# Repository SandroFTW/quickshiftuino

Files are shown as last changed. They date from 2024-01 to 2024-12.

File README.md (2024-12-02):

# quickshiftuino
## Latest development (edited 02.10.2024)
The third revision (R3) PCB is done and ordered. I added Molex Picoblade connectors to the board for two hall sensor connections without soldering. The dimensions increased slightly from 35x40mm to 42x40mm.
Vias are now also tented to prevent short circuits between Quickshiftuino PCB and the piggyback ESP32 Mini.
Currently I'm developing a hall pressure sensor that mounts at one end of the shift rod. 3D printed prototypes already give promising results, aluminium CNC milled parts are going to arrive in 2 weeks.

Gerber files will be available after I did some testing.

Previous R2 PCB that's almost the same as R3:

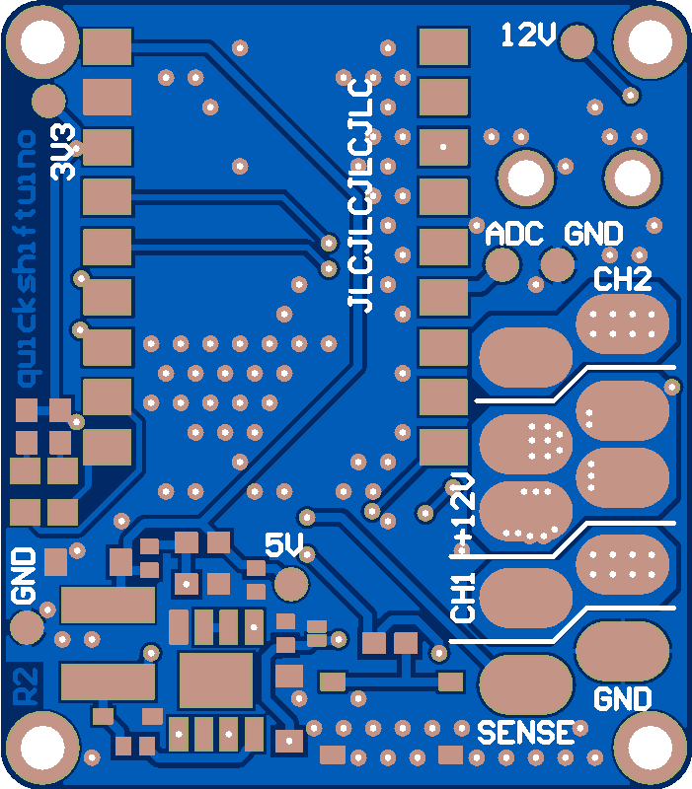
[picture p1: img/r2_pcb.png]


<br>

## Overview
Quickshiftuino is a simple device that detects the shift motion in the gear lever linkage and cuts the ignition coil power for a specified time.
This enables clutchless upshifting (and in some situations downshifting) by unloading the gearbox and drivetrain.

The cutoff time is dependant on engine RPM and is linearly scaled bewtween the lowest RPM (minRPM) and highest RPM (maxPRM).
An alternative to fixed cut-times would be a hall sensor and magnet mounted to the gearbox shift shaft to detect once the gearbox dog rings are touching or fully engaged.

My main idea was to keep it simple to use and universal. In total there are 6 possible configurations that have different advantages and disadvantages.

Configuration is possible though a locally hosted web-interface. Simply connect to the WiFi network provided by the device.
http://192.168.4.1/ gives access to the config page.
http://192.168.4.1/debug.html/ shows output values of the selected sensors and the current RPM value. This is helpful for finetuning parameters.

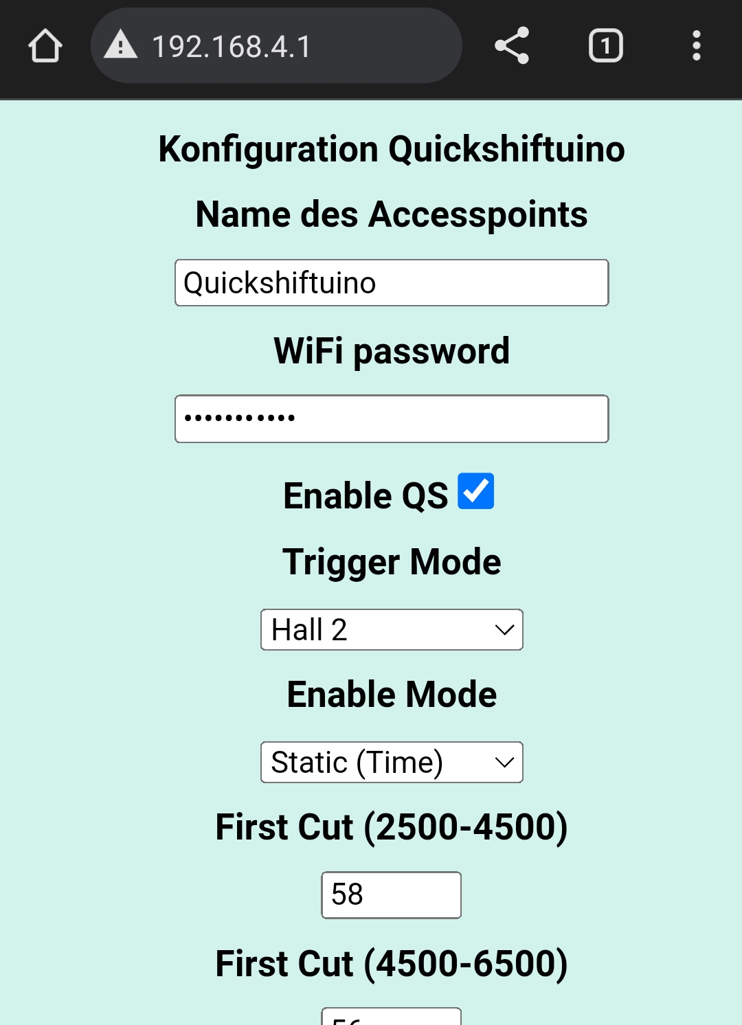
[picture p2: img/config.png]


<br>

The R1 PCB had a few issues with the power switching logic (high side P-MOS was wired incorrectly):

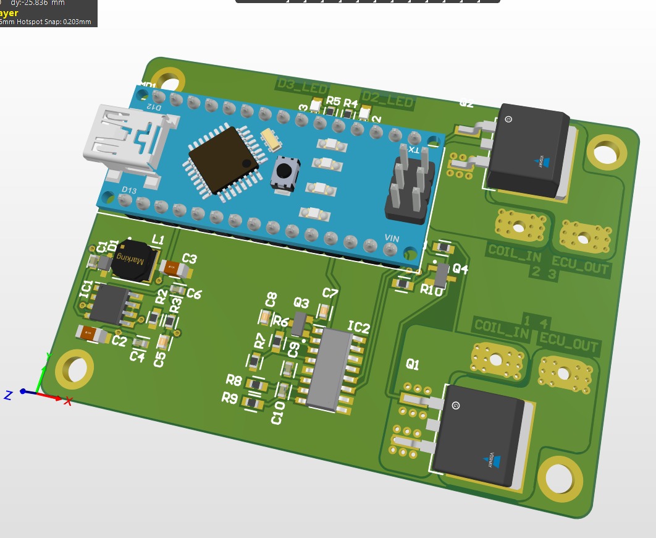
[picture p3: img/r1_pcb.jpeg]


For R2 many little bugs were resolved and the size drastically reduced.
The MCU was also switched from an Arduino Nano to a much more powerful and compact ESP32 Mini (Waveshare).

<br>

## Shift detection
Shift lever pressure can be measured in two different ways with quickshiftuino.

  ### 1. Piezo quickshifter sensor
  These sensors are all around Aliexpress if you search for quickshifter parts. A few big companies are using something similar with success already.
  This sensor doesn't react to force but it detects force change or momentum. The applied force can be more than enough but the sensor doesn't output a big voltage if you're shifting really soft and slow.
  The main drawback is that it only gives reliable results when mounted on the gearbox shaft clamp. That way there won't be a signal difference between up- and downshifts though. Installation is probably the easiest out of all.
  
  ### 2. Hall Sensor pressure sensor
  This is the latest option and still under development. Current tests show really good results and easy setup. The required parts are a bit pricier than the Piezo sensor though. A hall sensor measures the movement of a spring loaded mechanism that's mounted in the shift rod. Due to it being fairly low profile a modification of the shift rod might not be required on many bikes.

  ### 3. Load cell (not supported yet)
  The PCB features an HX711 load cell amplifier circuit.
  A DYMH-103 load cell needs to be installed in the shift rod to sense actual force.
  This method is more complex since in most cases the shift rod needs to be cut and modified but you will also get more consistent results.
  Another benefit is that up- and downshifts are clearly distinguishable because of positive and negative readings.

<br>

## Future plans
  ### Software ToDo's
  - Add hysteresis for hall sensor pressure sensor to prevent continuous triggering when holding the shift lever up in top gear
  - Instead of measuring ignition pulses in a fixed timespan: Set up timer that resets with each ignition pulse (RPM way more precise and faster update rate)
  - Long term: Improve efficiency of config GUI code and move all non-quickshifter tasks to second MCU core (enables faster loop times, probably not necessary)
  - Fun project: 2-step RPM limiter for launch control or just cool flames out of the exhaust (relies on quick and precise RPM measurement)
  - Fun project: Add support for shift indicator LED using free GPIO pad on R3 PCB (could also be used for other practical indicators)
  ### Hardware
  - Use N-Mos instead of P-Mos (requires high side driver, e.g. DZDH0401DW-7, current total voltage drop ~0.3V, maybe 0.1V possible)

The current design might cause unwanted pre-ignition if the coil power is cut during the dwell time. I haven't noticed this happening but there would be 2 approaches to prevent this:
- Switch to a N-Mos pull down design that overrides the ECU signal and keeps the coil pulled low (less complicated wiring but more heat/current in the coil)
- Only allow ignition cuts for a certain time after the coil has fired (maybe even RPM based, keeps current hardware)
  
Currently I am working on the second revision of the PCB which will have a few major issues resolved (mainly power switching logic).
I'm also thinking about either switching to an ESP32 MCU or adding a bluetooth module to the PCB. This should enable changing configuration values without the need for a computer and Arduino IDE.

The V1 PCB design will be added and I will upload a few pictures and videos of the project in a few weeks.

First test in the garage as a proof of concept: Video[https://youtu.be/FZ6roKEg_gY]

## Dependencies
- ESPAsyncWebServer (https://github.com/me-no-dev/ESPAsyncWebServer)
- AsyncWebConfig (https://github.com/GerLech/AsyncWebConfig/)
- AsyncTCP (https://github.com/dvarrel/AsyncTCP)
- WebSockets (https://github.com/Links2004/arduinoWebSockets)

AsyncWebConfig requires changing MAXVALUES in the header file from 20 to 30!; https://github.com/GerLech/AsyncWebConfig/blob/main/src/AsyncWebConfig.h#L32
Don't use the ESPAsyncWebServer from the library manager, you need to manually install the one by me-no-dev.

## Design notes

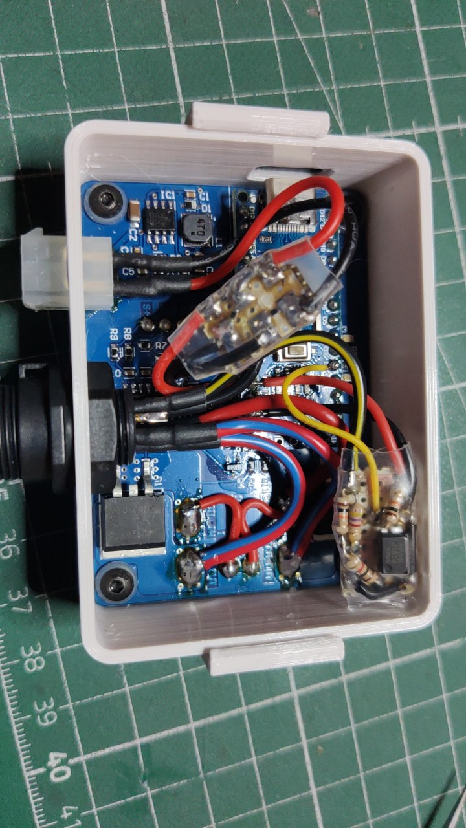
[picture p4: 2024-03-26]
img/r1_electronics.jpg

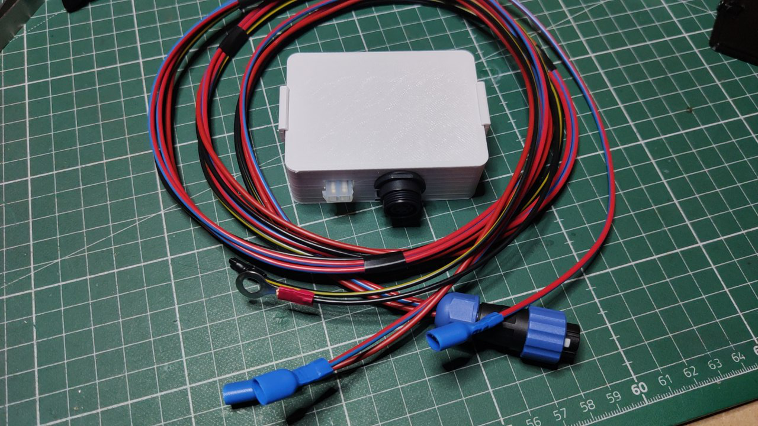
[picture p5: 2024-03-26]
img/r1_harness.jpg

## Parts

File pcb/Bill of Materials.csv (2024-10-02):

Comment | Description | Designator | Quantity
PC81710NIP1B | Attenuator or Isolator | AT1 | 1
C0603C104K3PACTU | C0603 0.10 µF X5R 30ppm/°C 10.00% 25 V | C1, C4, C6, C9, C10 | 5
C3216X5R1E476M160AC | Multilayer Ceramic Capacitors 47uF ±20% 25V X5R SMD 1206 | C2, C3 | 2
C0603C225K4PACTU | CAP CER 2.2UF 16V X5R 0603 | C5 | 1
C0603C106M8PACTU | CAP CER 10UF 10V X5R 0603 | C7, C8 | 2
C0603C333K1RECAUTO | C0603C333K1RECAUTO 0603 (1608METRIC) Ceramic Capacitor Esd SMD Auto X7R 100V 0.033MUF ±10% X7R | C11 | 1
C0603C473K3RACTU | CAP CER 0.047UF 25V 10% X7R 0603 | C12 | 1
CL10A105KA8NNNC | Cap Ceramic 1uF 25V X5R ±10% Pad SMD 0603 +85°C T/R | C13, C14 | 2
BAT165 | Medium Power AF Schottky Diode, SOD323, Reel, Green | D1 | 1
150080RS75000 |  | D2 | 1
150080GS75000 |  | D3 | 1
D20V0L1B2WS-7 | TVS Diode (Bi-directional) | D4, D7, D8 | 3
824521331 | 824521331 TVS diode [Würth Elektronik] 824521331 TVS diode | D5, D6 | 2
MP9486GN-Z | Integrated Circuit | IC1 | 1
HX711 | Integrated Circuit | IC2 | 1
Waveshare ESP32-S3 Mini | WaveShare ESP32-S3 Mini Development Board ESP32-S3FH4R2 240MHz 2.4GHz Wi-Fi Bluetooth 5 | IC4 | 1
53261-0371 | CONN HEADER SMD R/A 3POS 1.25MM | J1, J2 | 2
74404052470 | 74404052470 Inductors, Fixed, WE-LQS SMD 5020 47uH 0.8A 521mOhms | L1 | 1
SQJ459EP-T1_GE3 | MOSFET P-CH 60V 52A POWERPAKSO-8 | Q1, Q2 | 2
MMBT4403LT1G | Switching Transistor, PNP Silicon, 3-Pin SOT-23, Pb-Free, Tape and Reel | Q3 | 1
2N7002 | N-Channel OptiMOS Small-Signal-Transistor, 60 V VDS, 0.3 A ID, -55 to 150 degC, PG-SOT23, Reel, Green | Q4, Q5 | 2
CRCW060310K0FKEC | RES Thick Film, 10kO, 1%, 0.1W, 100ppm/°C, 0603 | R1, R2, R6, R10, R11, R12, R13, R16, R18, R19, R21 | 11
CRCW0603240KFKEA | RES Thick Film, 240kO, 1%, 0.1W, 100ppm/°C, 0603 | R3 | 1
CRCW0603100RFKEB | RES Thick Film, 100O, 1%, 0.1W, 100ppm/°C, 0603 | R4, R5, R8, R9 | 4
CRCW06038K20FKEC | RES Thick Film, 8.2kO, 1%, 0.1W, 100ppm/°C, 0603 | R7 | 1
CRCW06033K30FKEA | RES Thick Film, 3.3kO, 1%, 0.1W, 100ppm/°C, 0603 | R14, R22 | 2
0 Ohm Jumper | RES Thick Film, 0O, 5%, 0.33W, 200ppm/°C, 0603 | R15 | 1
RMCF0603FT2K20 | 2.2kO ±1% 0.1W 0603 Thick Film Chip Resistor AEC-Q200 compliant | R17 | 1
CRCW06032M00FKEA | RES Thick Film, 2MO, 1%, 0.1W, 100ppm/°C, 0603 | R20 | 1
CRCW060320K0FKEA | RES Thick Film, 20kO, 1%, 0.1W, 100ppm/°C, 0603 | R23, R24 | 2

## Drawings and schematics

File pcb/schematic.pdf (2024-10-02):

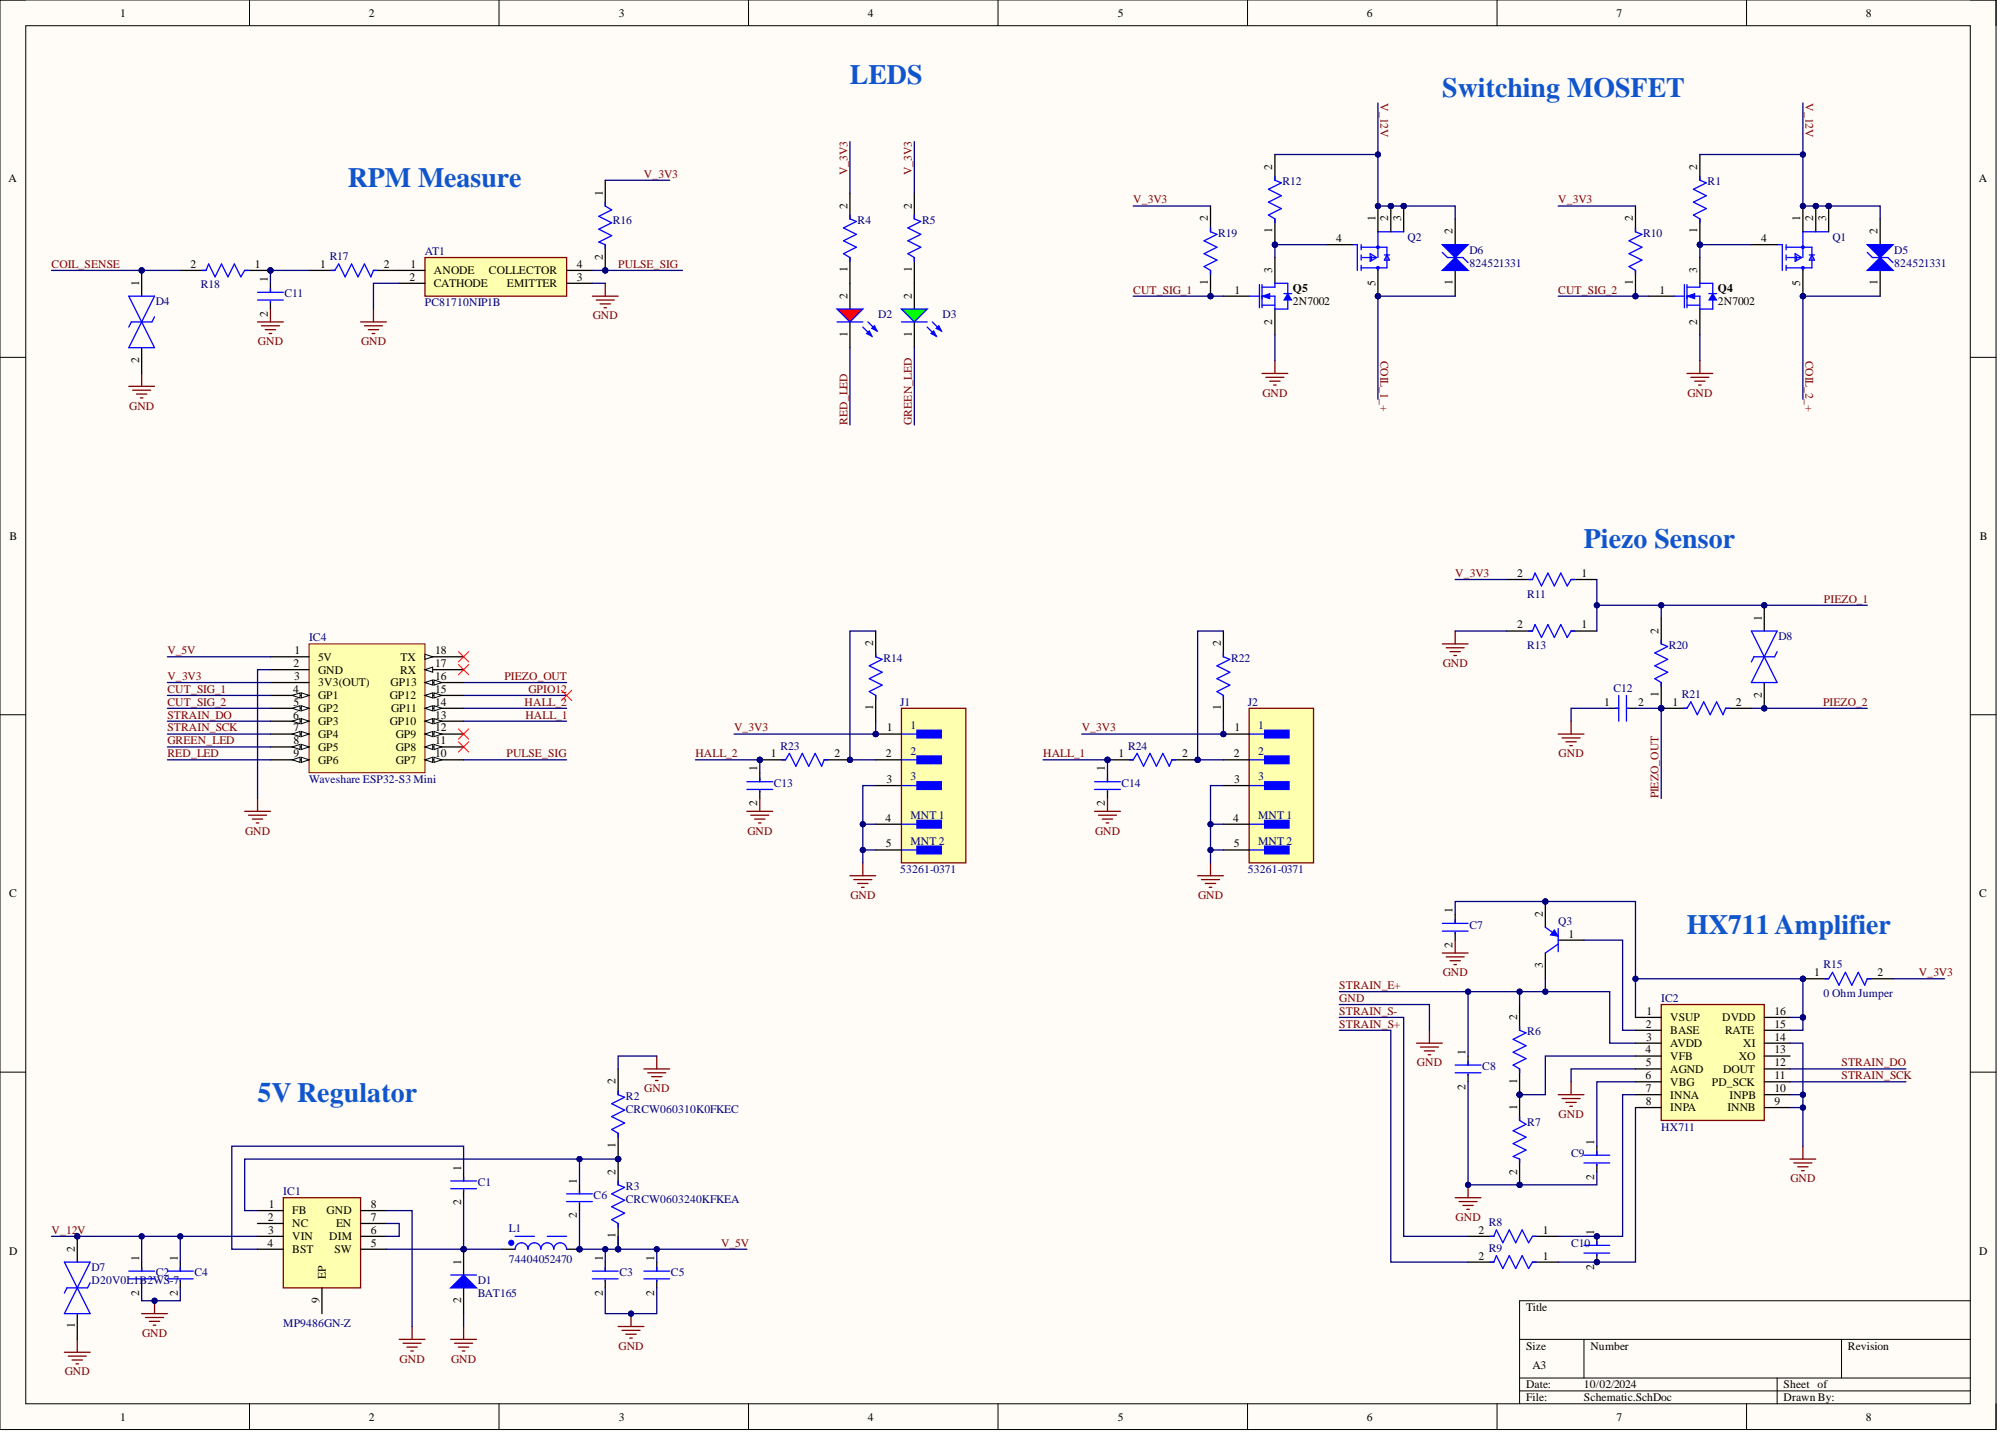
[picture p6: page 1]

VBG 6
INNA 7
INPA 8

GND C9

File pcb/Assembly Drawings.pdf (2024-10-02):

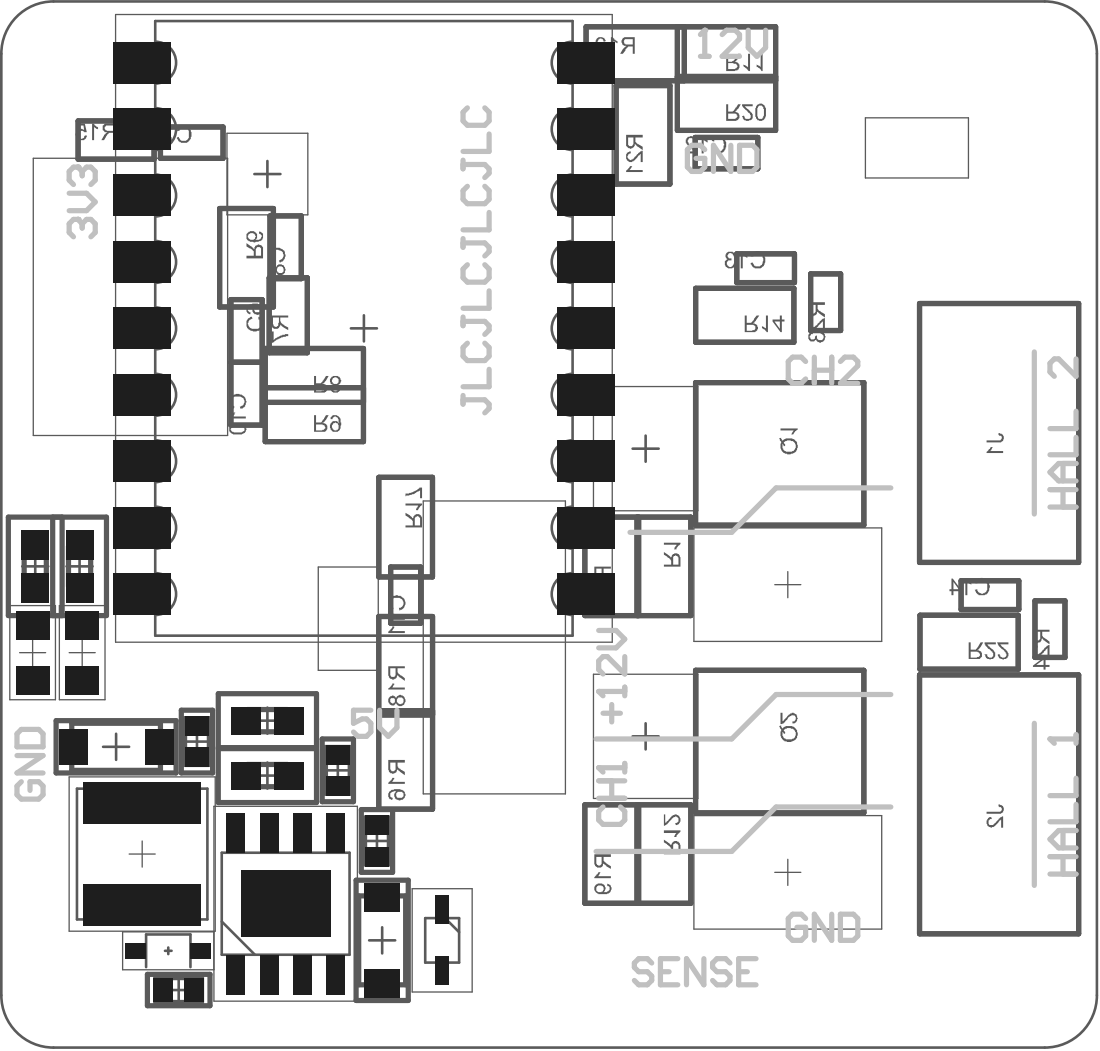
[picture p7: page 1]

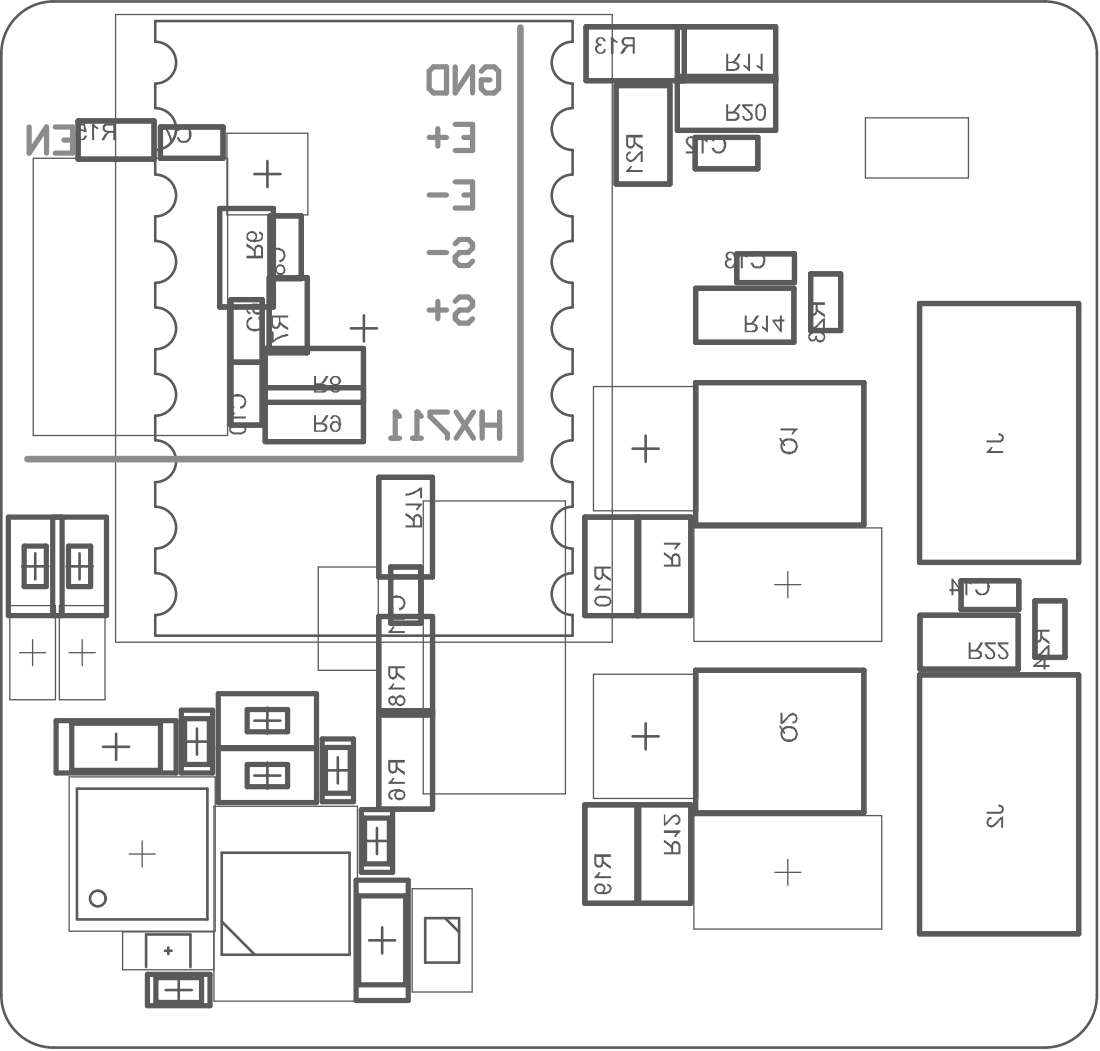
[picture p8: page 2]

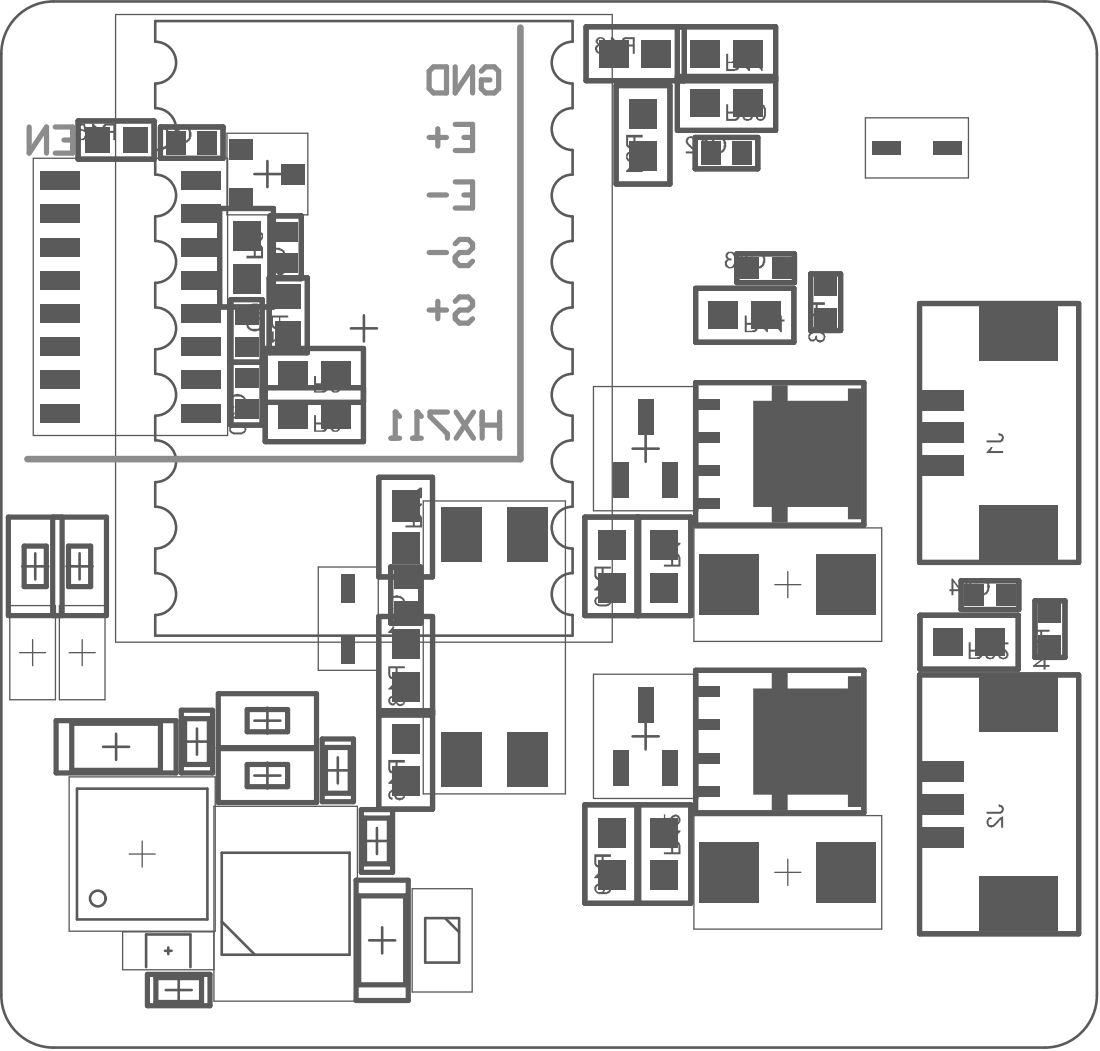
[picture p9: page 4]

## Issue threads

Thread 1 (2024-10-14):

SPECIFIC

Riccardo-Adami, 2024-10-14:
/I wanted to do the same, can i do the same using areduino nano or arduino one? what calbs do i need? how can i implement the logic of the button when pressed? how can i return energy to the candle and other few questions, thanks for your time.
(i can write you on email if i can find one).

SandroFTW, 2024-10-14:
Hi,
you can take a look at the R1 release files and schematic. R1 used an Arduino Nano and worked totally fine.

I assume "button" refers to the sensor that detects the upshift motion? The easiest way to add that is the piezo sensor listed in the readme file. It only requires one screw to be changed and no further modifications to the bike.

Quickshiftuino uses a pMOS right now to simplify the circuit. In theory an nMOS with a driver circuit would reduce the losses due to resistance but the coil only draws ~10-15A usually which is less than 0.3V voltage drop (from your 12V battery voltage). Might be a consideration for the future to change that.

Feel free to ask if you have further questions.

Riccardo-Adami, 2024-10-14:
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

thank you very much for the quick answer, I was wondering if on a bike with less power and no rods, it would still be okay. By “button” I was referring to a button/sensor placed under the shift lever tip that would send a signal to the arduino (arduino one or arduino nano, what do you recommend?) and this would interrupt for a temppo timespan (like 70 milliseconds) the current given to the spark plug, and once the 70 milliseconds was over it would resume the current flow
Still thx for the clear response :)

SandroFTW, 2024-10-15:
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

What you're describing would be the absolute minimum requirements.
A button is probably not enough for smooth operation. You need a sensor that only triggers once a certain force is applied to the shift lever so it's preloaded (~5-10kg on the lever).
[Piezo pressure sensor](https://aliexpress.com/item/1005004447507076.html) & [Fitting Connector, 2p](https://aliexpress.com/item/1005001706480040.html)
This is the sensor I suggest. If you place this on the clamping part that attaches the shift lever to the gearbox shaft you get a signal based on the force you apply to the lever.

Once it senses enough preload pressure you can cut the power for 70ms and it will probably shift without issues.
It probably won't be very smooth though. On my bike (Yamaha XJ6 4 cylinder) the optimal time is between 54ms for low RPM and 62ms for high RPM. A few ms difference already make quite a difference. That's why I'm changing the time based on RPM.

To get it really smooth you can also use a hall sensor that measures the position of the gearbox shaft. This indicates once the gear is fully engaged and tells the arduino to enable power again.

Riccardo-Adami, 2024-10-15:
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

Yeah sure, thx a lot for the response. For the first model I ordered an Arduino Nano, relay, breadboard, a pressure button, just for a quick test. My moto is a single cylinder one, derby. I was thinking of putting it under the crank, so when it's pushed, only up, It will send a signal to the Arduino nano (I'm doing it with that, should i use the Arduino 1 instead?) and it will be connected to the relay which will turn off the power only when the button provides the signal, am I doing right? thx for ur time (:

SandroFTW, 2024-10-15:
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

Sounds good, Arduino Nano is fine. Make sure to include a dead time between power cuts or your engine will just switch of when finding neutral ^^

riccio8, 2024-10-15:
Yeah i was thinking about 20 mills, is it fine? btw the first test is only for up shifting, thx mate

SandroFTW, 2024-10-15:
> Yeah i was thinking about 20 mills, is it fine? btw the first test is only for up shifting, thx mate (that's my main account sry )

Your single cylinder engine only fires about every 50 ms assuming 1200 RPM idle. So there's a high change it just doesn't notice the 20ms power on.

I have it at 350ms which is just a bit less than the fastest interval that I'm upshifting.

riccio8, 2024-10-15:
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

yeh yeah I meant it, 350ms aren't too much? just asking, I was thinking of doing it with 70ms per up shifting (is it is okay Right?) and 20 between the number of the up shifting

SandroFTW, 2024-10-15:
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

Sorry if I wasn't precise enough.

After you press the button it should wait for ~20ms until disabling power, then disable for ~70ms. After enabling it shouldn't react to another button press for ~350ms so it doesn't get stuck in a loop and kill the engine for example if you're in top gear and holding the lever up. Also a flag that disables another cutoff interval if you haven't released the lever yet is helpful.

Just sharing my experience since I already came across all these bugs in the last year that I've been working on this project :p

riccio8, 2024-10-15:
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

yeah yeah thx a lot, you were very clear and complete. Now I will see how the project goes and if I have other doubts I will definitely write to you, thank you very much

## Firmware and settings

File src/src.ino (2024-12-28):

#include <WebSocketsServer.h>
#include <ESPAsyncWebServer.h>
#include <AsyncWebConfig.h>
#include <AsyncTCP.h>
#include <SPIFFS.h>
#include <WiFi.h>

// TODO: Check if lever moved from zero position after 20 ms otherwise cancel shift
// -> Almost done, add more config options for tuning

// waitHyst feature not compatible with piezo sensor

// Make LED functions more useful (green led shift pressure indicator, red led rpm)

WebSocketsServer webSocket = WebSocketsServer(81);

// MAIN CONFIGURATION
#define loopTime         2    // 500 Hz

// PIN DEFINES
#define GREEN_LED 5
#define RED_LED   6
#define IGN_FET_1 1
#define IGN_FET_2 2
#define PIEZO_PIN 13
#define HALL1_PIN 10 // Hall Sensor 1 (Gearbox Position)
#define HALL2_PIN 11 // Hall Sensor 2 (Shift pressure)
#define RPM_PIN   7

// GLOBAL VARIABLES
static unsigned long lastCutMillis = 0;   // Time of last ignition cut begin
static unsigned long currMillis = 0;      // millis()
static unsigned long lastMillis = 0;      // Last cycle millis() (currMillis - loopTime)
static unsigned int coilsDisabled = 0;    // Is ignition currently disabled?
static bool waitHyst = true;              // pressure sensor hysteresis
static int currRpmRange = 0;              // 0-4 to choose cutoffTime from array
volatile bool redLED = false;             // Used to toggle red LED on RPM pulse
volatile bool greenLED = false;           // Used to indicate position sensor state

static int pressureValue = 0;
static int gearboxValue = 0;

hw_timer_t *Timer0_Cfg = NULL; // LED blink
volatile int cycleCounter = 0;

volatile float lastRPM = 0;
volatile float quickRPM = 0;
volatile uint8_t average_count = 0;
hw_timer_t *Timer1_Cfg = NULL; // RPM

String params = "["
  "{"
  "'name':'password',"
  "'label':'WiFi password',"
  "'type':"+String(INPUTPASSWORD)+","
  "'default':''"
  "},"
  "{"
  "'name':'enable',"
  "'label':'Enable QS',"
  "'type':"+String(INPUTCHECKBOX)+","
  "'default':'1'"
  "},"
  "{"
  "'name':'trigmode',"
  "'label':'Trigger Mode',"
  "'type':"+String(INPUTSELECT)+","
  "'options':["
  "{'v':'0','l':'Piezo'},"
  "{'v':'1','l':'Piezo (Inverted)'},"
  "{'v':'2','l':'Hall 2'},"
  "{'v':'3','l':'Hall 2 (Inverted)'},"
  "{'v':'4','l':'Loadcell'}],"
  "'default':'2'"
  "},"
  "{"
  "'name':'enablemode',"
  "'label':'Enable Mode',"
  "'type':"+String(INPUTSELECT)+","
  "'options':["
  "{'v':'0','l':'Static (Time)'},"
  "{'v':'1','l':'Hall 1'},"
  "{'v':'2','l':'Hall 1 (Inverted)'}],"
  "'default':'1'"
  "},"
  "{"
  "'name':'cuttime_1',"
  "'label':'First Cut (2500-4500)',"
  "'type':"+String(INPUTNUMBER)+","
  "'min':0,'max':500,"
  "'default':'66'"
  "},"
  "{"
  "'name':'cuttime_2',"
  "'label':'First Cut (4500-6500)',"
  "'type':"+String(INPUTNUMBER)+","
  "'min':0,'max':500,"
  "'default':'64'"
  "},"
  "{"
  "'name':'cuttime_3',"
  "'label':'First Cut (6500-8500)',"
  "'type':"+String(INPUTNUMBER)+","
  "'min':0,'max':500,"
  "'default':'64'"
  "},"
  "{"
  "'name':'cuttime_4',"
  "'label':'First Cut (8500-10500)',"
  "'type':"+String(INPUTNUMBER)+","
  "'min':0,'max':500,"
  "'default':'62'"
  "},"
  "{"
  "'name':'cuttime_5',"
  "'label':'First Cut (10500-12500)',"
  "'type':"+String(INPUTNUMBER)+","
  "'min':0,'max':500,"
  "'default':'60'"
  "},"
  "{"
  "'name':'cutsmooth',"
  "'label':'Cut Smoothness',"
  "'type':"+String(INPUTSELECT)+","
  "'options':["
  "{'v':'0','l':'Very Hard (0 ms)'},"
  "{'v':'2','l':'Hard (4 ms)'},"
  "{'v':'4','l':'Medium (8 ms)'},"
  "{'v':'6','l':'Soft (12 ms)'},"
  "{'v':'8','l':'Very Soft (16 ms)'}],"
  "'default':'8'"
  "},"
    "{"
  "'name':'cutmax',"
  "'label':'Max Cut Time',"
  "'type':"+String(INPUTSELECT)+","
  "'options':["
  "{'v':'70','l':'Sporty (70 ms)'},"
  "{'v':'100','l':'Normal (100 ms)'},"
  "{'v':'150','l':'Slow (150 ms)'}],"
  "'default':'100'"
  "},"
  "{"
  "'name':'minrpm',"
  "'label':'Min RPM',"
  "'type':"+String(INPUTNUMBER)+","
  "'min':0,'max':20000,"
  "'default':'2500'"
  "},"
  "{"
  "'name':'maxrpm',"
  "'label':'Max RPM',"
  "'type':"+String(INPUTNUMBER)+","
  "'min':1000,'max':20000,"
  "'default':'12500'"
  "},"
  "{"
  "'name':'rpmmult',"
  "'label':'RPM Multiplier',"
  "'type':"+String(INPUTTEXT)+","
  "'default':'1.00'"
  "},"
  "{"
  "'name':'deadtime',"
  "'label':'Dead time (ms)',"
  "'type':"+String(INPUTNUMBER)+","
  "'min':0,'max':5000,"
  "'default':'350'"
  "},"
  "{"
  "'name':'cutsensitivity',"
  "'label':'Cut sensitivity (0-4095)',"
  "'type':"+String(INPUTNUMBER)+","
  "'min':0,'max':5000,"
  "'default':'950'"
  "},"
  "{"
  "'name':'cuthysteresis',"
  "'label':'Cut Hysteresis (0-4095)',"
  "'type':"+String(INPUTNUMBER)+","
  "'min':0,'max':5000,"
  "'default':'300'"
  "},"
  "{"
  "'name':'hallcenter',"
  "'label':'Hall centered (0-4095)',"
  "'type':"+String(INPUTNUMBER)+","
  "'min':0,'max':5000,"
  "'default':'1800'"
  "},"
  "{"
  "'name':'halltouching',"
  "'label':'Hall dogs touching (0-4095)',"
  "'type':"+String(INPUTNUMBER)+","
  "'min':0,'max':5000,"
  "'default':'2000'"
  "},"
  "{"
  "'name':'hallengaged',"
  "'label':'Hall gear engaged (0-4095)',"
  "'type':"+String(INPUTNUMBER)+","
  "'min':0,'max':5000,"
  "'default':'2200'"
  "},"
  "{"
  "'name':'twosteprpm',"
  "'label':'2-Step RPM (0=OFF)',"
  "'type':"+String(INPUTNUMBER)+","
  "'min':0,'max':20000,"
  "'default':'0'"
  "},"
  "{"
  "'name':'twostepcut',"
  "'label':'2-Step Cut (ms)',"
  "'type':"+String(INPUTNUMBER)+","
  "'min':1,'max':1000,"
  "'default':'40'"
  "},"
  "{"
  "'name':'beta',"
  "'label':'Beta Features',"
  "'type':"+String(INPUTCHECKBOX)+","
  "'default':'0'"
  "},"
  "{"
  "'name':'testmode',"
  "'label':'Test functionality',"
  "'type':"+String(INPUTCHECKBOX)+","
  "'default':'0'"
  "}"
  "]";

AsyncWebServer server(80);
AsyncWebConfig conf;

struct cfgOptions
{
  char ssid[32];
  char password[32];

  bool enable;

  int trigMode;      // 0 piezo, 1 piezo inv, 2 hall, 3 hall inv, 4 loadcell
  int enableMode;    // 0 static, 1 hall, 2 hall inv

  int cutTime[5];    // ms
  int cutSmooth;     // 0 very hard, 1 hard, 2 normal, 3 soft, 4 very soft
  int cutMax;        // 

  int minRPM;          // 1/min
  int maxRPM;          // 1/min

  float rpmMult;       // factor
  int deadTime;        // ms

  int cutSensitivity;
  int cutHysteresis;
  int hallCenter;
  int hallTouching;
  int hallEngaged;

  int twoStepRPM;
  int twoStepCut;

  bool beta;
  bool testmode;
} cfg;



void transferWebconfToStruct(String results)
{
    cfg.enable = conf.getBool("enable");

    cfg.trigMode = conf.getString("trigmode").toInt();
    cfg.enableMode = conf.getString("enablemode").toInt();

    cfg.cutTime[0] = conf.getInt("cuttime_1");
    cfg.cutTime[1] = conf.getInt("cuttime_2");
    cfg.cutTime[2] = conf.getInt("cuttime_3");
    cfg.cutTime[3] = conf.getInt("cuttime_4");
    cfg.cutTime[4] = conf.getInt("cuttime_5");

    cfg.cutSmooth = conf.getString("cutsmooth").toInt();
    cfg.cutMax = conf.getString("cutmax").toInt();

    cfg.minRPM = conf.getInt("minrpm");
    cfg.maxRPM = conf.getInt("maxrpm");

    cfg.rpmMult = conf.getFloat("rpmmult");
    cfg.deadTime = conf.getInt("deadtime");

    cfg.cutSensitivity = conf.getInt("cutsensitivity");
    cfg.cutHysteresis = conf.getInt("cuthysteresis");
    cfg.hallCenter = conf.getInt("hallcenter");
    cfg.hallTouching = conf.getInt("halltouching");
    cfg.hallEngaged = conf.getInt("hallengaged");

    cfg.twoStepRPM = conf.getInt("twosteprpm");
    cfg.twoStepCut = conf.getInt("twostepcut");

    cfg.beta = conf.getBool("beta");
    cfg.testmode = conf.getBool("testmode");
}

void handleRoot(AsyncWebServerRequest *request)
{
  conf.handleFormRequest(request);
  /*
  if (request->hasParam("SAVE"))
  {
    transferWebconfToStruct();
  }*/
}



// Create a task that will be executed on Core 0 (instead of 1)
TaskHandle_t Task1;
void push_debug(void *parameters)
{
  for (;;)
  {
    String broadcastString = String(pressureValue) + "," + String(gearboxValue) + "," + String(lastRPM) + "," + String(cfg.cutTime[currRpmRange]);

    webSocket.loop();
    webSocket.broadcastTXT(broadcastString);

    delay(50);
  }
}

// Interrupt Service Routine (ISR) for the timer
void IRAM_ATTR Timer0_ISR()
{
  if (cfg.testmode)
  {
    cycleCounter++;
    if (cycleCounter == 1)
    {
      greenLED = true;
      digitalWrite(GREEN_LED, greenLED);
      disable_ign();
    }
    else if (cycleCounter >= 10)
    {
      // Turn the LED OFF after 9 more cycles (total 5 cycles = 500ms)
      greenLED = false;
      digitalWrite(GREEN_LED, greenLED);
      enable_ign_1();
      enable_ign_2();
      cycleCounter = 0;  // Reset the cycle counter
    }
  }
  else if (!cfg.testmode && greenLED)
  {
    greenLED = false;
    enable_ign_1();
    enable_ign_2();
    cycleCounter = 0;
  }
}

// Timer configuration by ChatGPT lol
void setupTimer0(int frequency)
{
  // Detach timer to avoid conflicts
  if (Timer0_Cfg != NULL)
  {
    timerDetachInterrupt(Timer0_Cfg);
    timerEnd(Timer0_Cfg);
  }

  // Initialize timer (timer number 0, prescaler = 80, frequency in Hz)
  Timer0_Cfg = timerBegin(1000000); // Prescaler of 80 gives 1us resolution

  // Set the compare value based on the desired frequency
  int compareValue = 1000000 / (frequency); // *2 for toggling on both compare events

  // Set the timer to trigger interrupt at compare value
  timerAttachInterrupt(Timer0_Cfg, &Timer0_ISR);  // ISR on compare match
  timerAlarm(Timer0_Cfg, compareValue, true, 0);   // Set compare value and auto-reload
}



void disable_ign()
{
  digitalWrite(IGN_FET_1, LOW);
  digitalWrite(IGN_FET_2, LOW);
  //digitalWrite(GREEN_LED, LOW);
}

void enable_ign_1()
{
  digitalWrite(IGN_FET_1, HIGH);
}

void enable_ign_2()
{
  digitalWrite(IGN_FET_2, HIGH);
  //digitalWrite(GREEN_LED, HIGH);
}

void countPulse()
{
  digitalWrite(RED_LED, (redLED ? HIGH : LOW));
  redLED = !redLED;

  quickRPM = 60000000 / timerReadMicros(Timer1_Cfg) * cfg.rpmMult;

  if (average_count < 5)
  {
    average_count++;
    return;
  }

  lastRPM = ((5 * 60000000) / timerReadMicros(Timer1_Cfg)) * cfg.rpmMult;
  //lastRPM = 60000000 / timerReadMicros(Timer1_Cfg); //* cfg.rpmMult;
  timerWrite(Timer1_Cfg, 0);
  average_count = 0;
}



void setup()
{
  pinMode(GREEN_LED, OUTPUT); // Green LED
  pinMode(RED_LED, OUTPUT); // Red LED
  pinMode(IGN_FET_1, OUTPUT); // Ign Fet 1
  pinMode(IGN_FET_2, OUTPUT); // Ign Fet 2

  digitalWrite(GREEN_LED, HIGH);
  digitalWrite(RED_LED, HIGH);
  digitalWrite(IGN_FET_1, HIGH);
  digitalWrite(IGN_FET_2, HIGH);

  pinMode(PIEZO_PIN, INPUT); // Piezo Sensor
  pinMode(HALL1_PIN, INPUT); // Hall Sensor 1 (Gearbox Position)
  pinMode(HALL2_PIN, INPUT); // Hall Sensor 2 (Shift Pressure)

  Serial.begin(57600);

  // Interrupt routine for ingition pulse counting / RPM calculation
  pinMode(RPM_PIN, INPUT_PULLUP);
  attachInterrupt(RPM_PIN, countPulse, RISING);

  // Timer 1 initialisieren (Timer 1, Prescaler = 80 -> 1µs Auflösung)
  Timer1_Cfg = timerBegin(1000000); // Verwende Timer 1 mit 1 µs Auflösung

  conf.setDescription(params);
  conf.readConfig();
  transferWebconfToStruct("");

  WiFi.mode(WIFI_AP);
  WiFi.setTxPower(WIFI_POWER_7dBm);
  WiFi.softAP(conf.getApName(), conf.values[0].c_str());

  server.on("/", handleRoot);

  server.on("/debug.html", HTTP_GET, [](AsyncWebServerRequest *request) {
    request->send(SPIFFS, "/debug.html", "text/html");
  });

  conf.registerOnSave(transferWebconfToStruct);

  server.begin();
  webSocket.begin();

  setupTimer0(10);

  xTaskCreatePinnedToCore(push_debug, "CPU_0", 10000, NULL, 1, &Task1, 0);
}

void loop()
{
  currMillis = millis();

  if (currMillis >= (lastMillis + loopTime))
  {
    switch (cfg.trigMode)
    {
      case 0: // Piezo
        pressureValue = analogRead(PIEZO_PIN);
        break;

      case 1: // Piezo Inverted
        pressureValue = 4095 - analogRead(PIEZO_PIN);
        break;

      case 2: // Hall
        pressureValue = analogRead(HALL2_PIN);
        break;

      case 3: // Hall Inverted
        pressureValue = 4095 - analogRead(HALL2_PIN);
        break;

      case 4: // Loadcell
        pressureValue = 0;
        break;
    }

    // Only read ADC if Hall is selected as enable mode
    if (cfg.enableMode == 1 || cfg.enableMode == 2)
      gearboxValue = analogRead(HALL1_PIN);
    else
      gearboxValue = 0;

    lastMillis = currMillis;
  }

  // Skip all quickshifter features, only 2-step remains
  if (cfg.enable)
  {
    // If no new RPM value since 500ms set RPM to 0
    if (timerReadMicros(Timer1_Cfg) > 500000)
      lastRPM = 0;

    // pressure sensor value went below hysteresis, re-enable triggering
    if (pressureValue < (cfg.cutSensitivity - cfg.cutHysteresis))
      waitHyst = false;

    // RPM is below minRPM, shift lever needs to be released before an upshift is allowed when RPM climbs above minRPM
    if (lastRPM < cfg.minRPM)
      waitHyst = true;

    /* ######################### Shift pressure detection and ignition cut ######################### */
    // Disable ignition when pressure is sensed, sufficient RPM, deadTime passed and pressure was low before (hysteresis prevents continuous triggers when holding shift lever up in top gear)
    if (lastRPM >= cfg.minRPM && coilsDisabled == 0 && waitHyst == false && pressureValue >= cfg.cutSensitivity && currMillis >= (lastCutMillis + cfg.deadTime))
    {
      disable_ign();
      coilsDisabled = 2;
      waitHyst = true;
  
      currRpmRange = map(lastRPM, cfg.minRPM, cfg.maxRPM, 0, 4);
  
      lastCutMillis = currMillis;
    }

  
    // Enable ignition 1 when dog rings touching or time passed
    if (coilsDisabled == 2)
    {
      if ((cfg.enableMode == 0 && currMillis >= (lastCutMillis + cfg.cutTime[currRpmRange])) || ((cfg.enableMode == 1 || cfg.enableMode == 2) && gearboxValue >= cfg.hallTouching))
      {
        enable_ign_1();
        coilsDisabled = 1;
      }
    }
  
    // Enable ignition 2 when gear fully engaged or time + smooth passed
    if (coilsDisabled == 1)
    {
      if ((cfg.enableMode == 0 && currMillis >= (lastCutMillis + cfg.cutTime[currRpmRange] + cfg.cutSmooth)) || ((cfg.enableMode == 1 || cfg.enableMode == 2) && gearboxValue >= cfg.hallEngaged))
      {
        enable_ign_2();
        coilsDisabled = 0;
      }
    }

    // BETA - Enable ignition if gear lever hasn't left center position (upshifting in highest gear, hall enable mode only)
    // maybe a bool variable (e.g. cancelingCut is needed to prevent coil 1 from getting enabled after 30ms and then coil 2 after the regular cuttime)
    if (cfg.beta && coilsDisabled == 2 && (cfg.enableMode == 1 || cfg.enableMode == 2) && (gearboxValue <= cfg.hallCenter + abs(cfg.hallTouching - cfg.hallCenter)/2) && currMillis >= (lastCutMillis + 30))
    {
      enable_ign_1();
      coilsDisabled = 1;
    }
    if (cfg.beta && coilsDisabled == 1 && (cfg.enableMode == 1 || cfg.enableMode == 2) && (gearboxValue <= cfg.hallCenter + abs(cfg.hallTouching - cfg.hallCenter)/2) && currMillis >= (lastCutMillis + 30 + cfg.cutSmooth))
    {
      enable_ign_2();
      coilsDisabled = 0;
    }
  
    //Safety feature to prevent engine shutting off in case of an issue
    if (coilsDisabled == 2 && currMillis >= (lastCutMillis + cfg.cutMax))
    {
      enable_ign_1();
      coilsDisabled = 1;
    }
    if (coilsDisabled == 1 && currMillis >= (lastCutMillis + cfg.cutMax + cfg.cutSmooth))
    {
      enable_ign_2();
      coilsDisabled = 0;
    }
  }

  /* ######################### Two Step Rev Limiter ######################### */
  // (just for fun, WIP)
  if (cfg.twoStepRPM > 0)
  {
    if (coilsDisabled == 0 && quickRPM > cfg.twoStepRPM)
    {
      disable_ign();
      coilsDisabled = 2;
      lastCutMillis = currMillis;
    }
    else if (coilsDisabled > 0 && currMillis >= (lastCutMillis + cfg.twoStepCut))
    {
      enable_ign_1();
      enable_ign_2();
      coilsDisabled = 0;
    }
  }
}

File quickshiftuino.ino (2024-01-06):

// Uncomment to use load cell instead of piezo sensor
#define LOADCELL

// CHANGE CONSOLE DEBUG OUTPUT
//#define DEBUG_SENSOR
  #define DEBUG_SHIFT
//#define DEBUG_RPM

#ifdef LOADCELL
  #include <HX711_ADC.h>
  #include <EEPROM.h>

  #define calAdressEEPROM 0
  #define tareAdressEEPROM 4

  #define HX711_DOUT 4 // MCU -> HX711 Dout Pin
  #define HX711_SCK  5 // MCU -> HX711 SCK Pin
#elif
  #define PIEZO_SENSOR    19 // A5  (Piezo Sensor Pin)
#endif

// QUICKSHIFTER CONFIGURATION
#define loopTime         5    // 200 Hz
#define rpmLoopTime      200  // 5 Hz

#define cutTimeMax       100  // 100 ms at minRPM
#define cutTimeMin       85   // 85 ms at maxRPM

#define minRPM           3000  // min. required RPM to allow QS 
#define maxRPM           12000 // Engine RPM for minCutTime (still works above maxRPM, cutTime is always cutTimeMin)

#define delayTime        25   // 25 ms (delay after trigger force is reached)
#define deadTime         300  // 300 ms (dead time before next cut)
#define rpmFactor        60 * ((1000 / rpmLoopTime))

// SENSITIVITY VALUES
#ifdef LOADCELL
  #define cutSensitivity   5000  // ~ 5000 g on the load cell
#elif
  #define cutSensitivity   200   // min. piezo force threshold
#endif

// PIN DEFINES
#define CUT_SIG   10 // D10 (Ignition cut MOSFET pin)
#define GREEN_LED 3  // D3
#define RED_LED   2  // D2

// GLOBAL VARIABLES
static unsigned long lastPulseMillis = 0; // Time of last RPM calculation
static unsigned long lastCutMillis = 0;   // Time of last shiftQueued
static unsigned long currMillis = 0;      // millis()
static unsigned long lastMillis = 0;      // Last cycle millis() (currMillis - loopTime)
static volatile int pulseCount = 0;       // Ignition interrupt count since last RPM calculation
static bool ignitionDisabled = false;     // Is ignition currently disabled?
static bool shiftCooldown = true;         // Is QS on cooldown after last shift?
static bool shiftQueued = false;          // Is shiftQueued because threshold was reached?
static float cutTime = 0;                 // Calculated cutTime based on RPM
static float lastRPM = 0;                 // Last calculated RPM

#ifdef LOADCELL
  HX711_ADC LoadCell(HX711_DOUT, HX711_SCK);
  static float sensorValue = 0;
#elif
  static int sensorValue = 0;
#endif

// CALCULATE CUTOFF TIME BASED ON ENGINE RPM
int cutoffTime()
{
  if (lastRPM > maxRPM)
  {
    return cutTimeMin; // If RPM is above maxRPM always use cutTimeMin
  }
  else
  {
    return map(lastRPM, minRPM, maxRPM, cutTimeMax, cutTimeMin); // Scales cutoffTime based on RPM (more RPM -> shorter cut)
  }
}

void disable_ign()
{
  //PORTB |= (0 << 2); // Disable Ignition
  //PORTD |= (1 << 3); // Enable Green LED
  digitalWrite(CUT_SIG, LOW);
  digitalWrite(GREEN_LED, HIGH);
}

void enable_ign()
{
  //PORTB |= (1 << 2); // Enable Ignition
  //PORTD |= (0 << 3); // Disable Green LED
  digitalWrite(CUT_SIG, HIGH);
  digitalWrite(GREEN_LED, LOW);
}

void countPulse()
{
  pulseCount++;
}

int updatePiezoValue()
{
  if (currMillis >= (lastMillis + loopTime))
  {
    sensorValue = analogRead(PIEZO_SENSOR) - 512;
    lastMillis = currMillis;

    #ifdef DEBUG_SENSOR
      Serial.print(currMillis); Serial.print(" - sensorValue: "); Serial.println(sensorValue);
    #endif

    #ifdef DEBUG_SENSOR_PLOT
      Serial.print("min:-512,max:512,sensorValue:"); Serial.println(sensorValue);
    #endif
  }
}

float updateLoadcellValue()
{
  if (LoadCell.update())
  {
    sensorValue = LoadCell.getData();
    lastMillis = currMillis;

    #ifdef DEBUG_SENSOR
      Serial.print(currMillis); Serial.print(" - sensorValue: "); Serial.println(sensorValue);
    #endif

    #ifdef DEBUG_SENSOR_PLOT
      Serial.print("min:-20000,max:20000,sensorValue:"); Serial.println(sensorValue);
    #endif
  }
}



void setup()
{
  pinMode(GREEN_LED,    OUTPUT);
  //pinMode(RED_LED,      OUTPUT);
  pinMode(CUT_SIG,      OUTPUT);

  digitalWrite(GREEN_LED, LOW);
  //digitalWrite(RED_LED,   HIGH);
  digitalWrite(CUT_SIG,   HIGH);

  Serial.begin(57600);

  #ifdef LOADCELL
    LoadCell.begin();

    float calibrationValue; // = 75.2 for gramms
    long tareValue;
    EEPROM.get(calAdressEEPROM, calibrationValue);
    EEPROM.get(tareAdressEEPROM, tareValue);

    Serial.print("calValue: "); Serial.print(calibrationValue); Serial.print(" - tareValue: "); Serial.println(tareValue);

    LoadCell.start(stabilizingTime, false); // Set to true to enable tare on power-up

    if (LoadCell.getTareTimeoutFlag()) { Serial.println("MCU>HX711 timeout"); while (1); }
    else { // HX711 connection successful
      LoadCell.setCalFactor(calibrationValue);
      PORTD |= (0 << 3); // Disable Green LED when startup is complete -> digitalWrite(GREEN_LED, LOW);
    }
  #elif
    pinMode(PIEZO_SENSOR, INPUT);
  #endif

  // Interrupt routine for ingition pulse counting / RPM calculation
  /*
  DDRD &= ~(1 << 2); // Set D2 as input pin
  PORTD |= (1 << 2); // Enable internal pullup for D2
  attachInterrupt(0, countPulse, RISING); // D2 as Interrupt
  */
}
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

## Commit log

2024-01-09 rename arduino code file
2024-01-16 Add R1 PCB files
    This is almost R1, just with a few small adjustments
    [Quickshiftuino R1.PrjPcb, Schematic R1.SchDoc]
2024-04-21 Add Hall Gear Sensor
    First version of Hall compatibility. The sensor is mounted on the gear lever to detect when the gear is fully engaged. This eliminates the need for fixed cutoff times and should be way smoother.
    [src.ino]
2024-08-11 upload R2 code, gerber and assembly data
    [PCB.GBL, PCB.GBO, PCB.GBP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]
2024-10-02 R2 PCB files and latest code
    [Bill of Materials.csv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]
2024-10-29 New RPM algorithm, cleaner config
    - RPM measurement by measuring time between ignition pulses
    - More dropdown options with description instead of integer input fields
    - reduced number of config options for easier understandability
    - fixed 2-step RPM limiter (use 20-50ms at 3000-7000 RPM roughly for cool results, at least on 600cc 4cyl)
    [src.ino]
